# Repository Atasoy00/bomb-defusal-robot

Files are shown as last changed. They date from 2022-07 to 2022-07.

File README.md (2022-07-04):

Bomba İmha Robotu v1.0
======

Bu projede 5 DOF robot kol barındıran hareketli bir sistem tasarımı yapılmıştır.



## # Robot Kol

- Robot kol 5 DOF hareket eksenine sahiptir.
- Ana ve ara eklem servolarının hareketinde ters kinematik denklemler kullanılmıştır.
- Robot kolun gövde bağlantı bölümünde bir adet rulman kullanılarak sistem bu rulman üzerine oturtulmuştur
- Küçük güçte bir servo kullanılarak tüm sistem rahatça döndürülebilmektedir.
- Robot kol 200g'a kadar ağırlıktaki yükleri sorunsuz kaldırabilmektedir



## # Palet

- Motorlardan palete 1:256 oranlı redüktör tasarlanmıştır.
- Yüksek güç üreten redüktör için 30 parça kaymaz palet tasarlanmıştır.
- 6x2 destek tekerleri ile palet sabitlenmiştir.
- Sistemin gücü 12V 9600 rpm çift motorla sağlanmaktadır.  



## # Kontrol Seçenekleri

### 1. TCP Bağlantısı ile Gamepad Kontrolü

- Robot başlatılmadan önce RC kumanda kapalı ise TCP ağına bağlanır.
- TCP/IP bağlantısı kullanılarak gönderilen mesaj kontrol edilmektedir.
- Statik IP adresi kullanılarak adres sabitlenmiştir.
- PC üzerinden kontrol için Python ile TCP kontrol uygulaması yazılmıştır.
- Bilgisayar klavyesinin yetersizliğinden dolayı gamepad driver'ı eklenmiştir.
- Gamepad üzerinden alınan kontroller bir mesaj haline getirilerek gönderilmektedir.



### 2. RC Kumanda Kontrolü

- Robot başlatılmadan önce kumanda açık ise RC kumanda üzerinden kontrol alır.
- Kullanıcıya kontrol alternatifi sunularak RC alıcı entegre edilmiştir.
- RC Kumanda 2km'ye kadar kontrol mesafesini desteklemektedir.
- Kumandadan verilen kontroller daha hızlı ve doğrudur.
- Kumanda üzerinde yeterince kontrol kanalı olmadığı için switch ile sürüş ve robot kol modları arasında geçiş yapılabilmektedir.
- Ters kinematik özelliği kumanda üzerinden açılıp kapanabilmektedir. 



## # Elektronik Devre Şeması



## # Üretim

Projede kullanılan tüm parçalar piyasada kolayca bulunabilen fiyat performans ürünleridir. Geri kalan parçalar açık kaynaklı şekilde proje dosyalarında .stl formatında sunulmuştur. 3B baskı yöntemleri ile parçalar elde edilebilir, hatta eklemeler yapılarak farklı görevlere yönelik tasarımlar oluşturulabilir. Gerekli parçaların üretimi ve temini sonrası kolayca bir araya getirilebilir ve kodu yüklenerek çalışır hale getirilebiliir. 



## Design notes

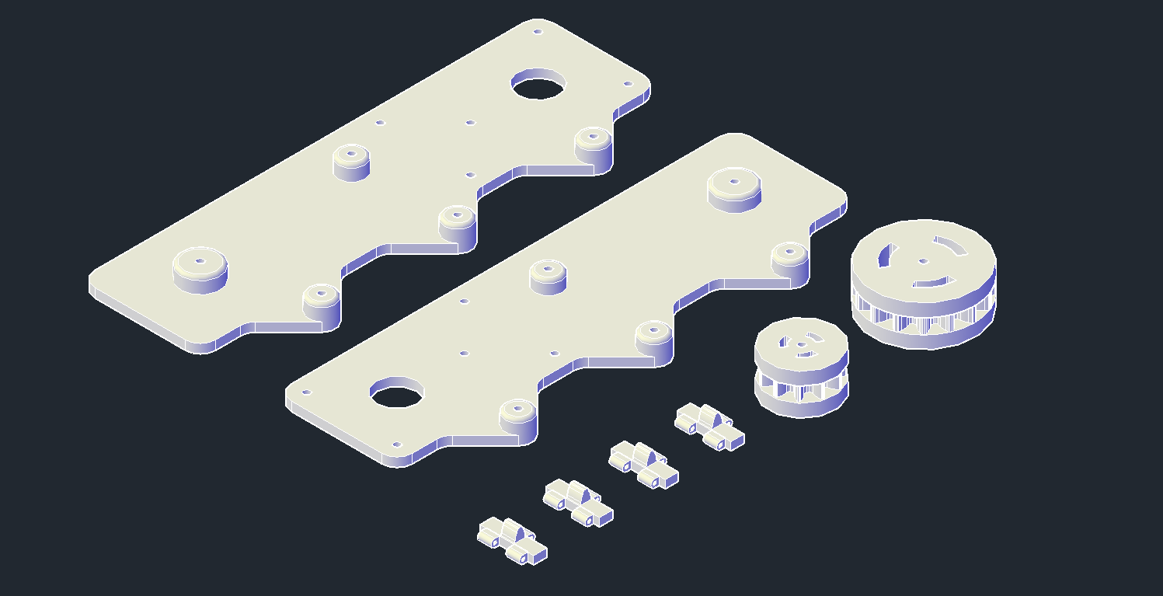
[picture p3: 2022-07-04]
Modellemeler/Resimler/palet_sistemleri.png

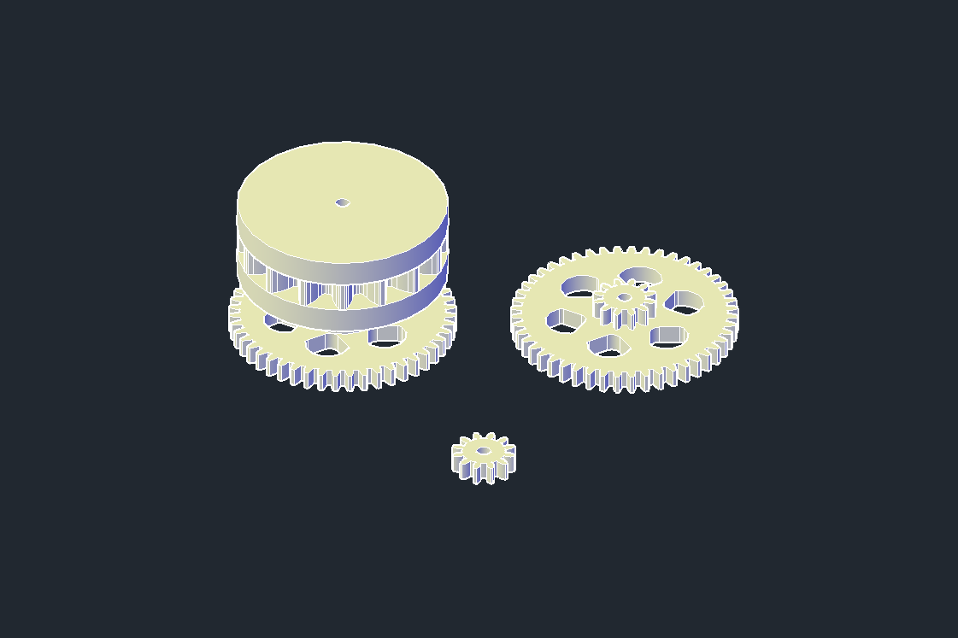
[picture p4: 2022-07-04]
Modellemeler/Resimler/bykdişli_kçkdişli_anatekerdişlisi.png

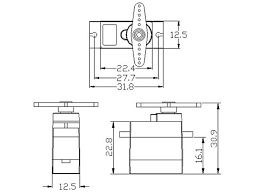
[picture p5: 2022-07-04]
Yardımcı/sg90-teknik çizim.jpg

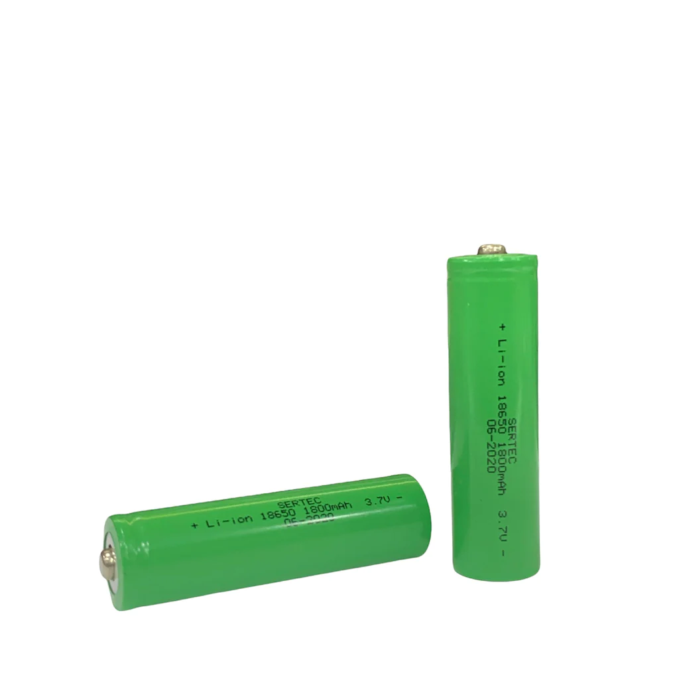
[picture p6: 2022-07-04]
Malzemeler/Resimler/1800mAh 18650 Li-on Pil.jpg

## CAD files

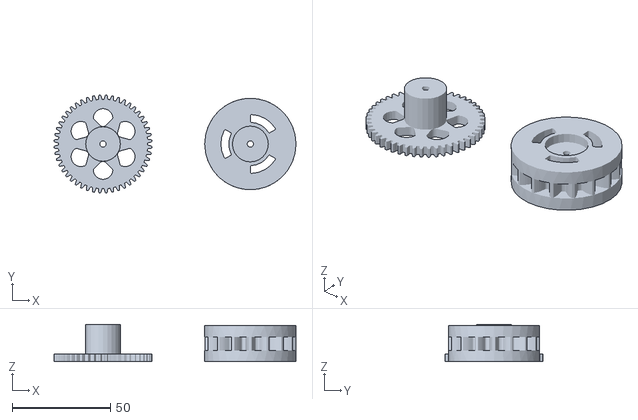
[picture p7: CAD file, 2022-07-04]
Modellemeler/PaletDişliTeker.stl
123.2 x 49.9 x 19.0

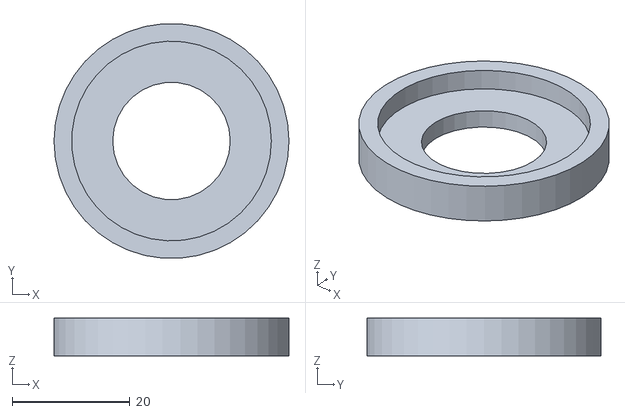
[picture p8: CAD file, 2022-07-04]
Modellemeler/Rulman Şasisi/Rulman Şasisi üst .stl
40.0 x 39.9 x 6.40

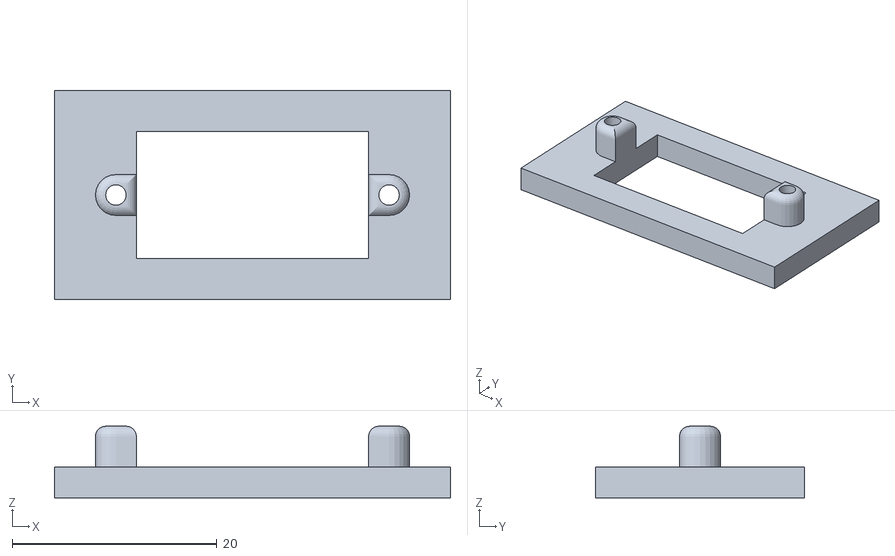
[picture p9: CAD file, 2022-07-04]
Modellemeler/Servo Ekipmanları/Servo Tutucu dnm1.stl
38.7 x 20.4 x 7.00

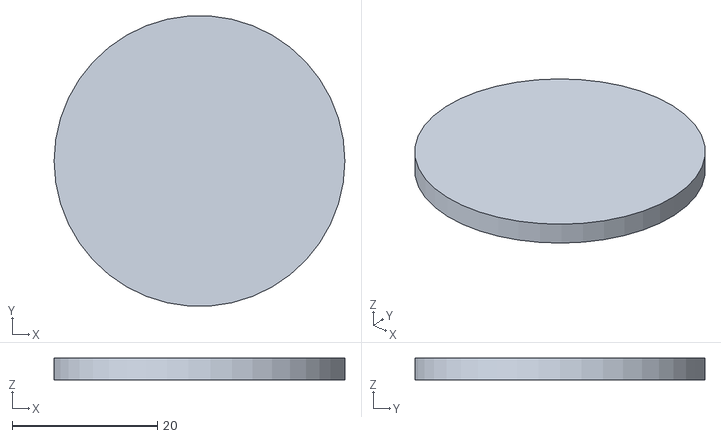
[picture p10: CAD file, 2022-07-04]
Modellemeler/Rulman Şasisi/Rulman Şasisi üst kapak.stl
40.0 x 39.9 x 3.00

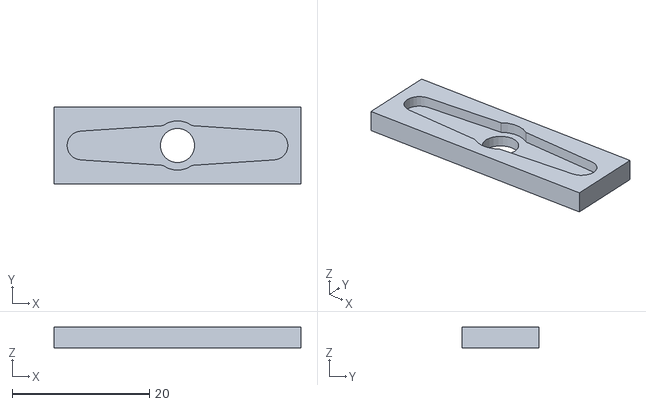
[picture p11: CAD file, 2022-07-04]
Modellemeler/Servo Ekipmanları/Servo Ucu 2 eksen dnm1.stl
36.0 x 11.2 x 3.00

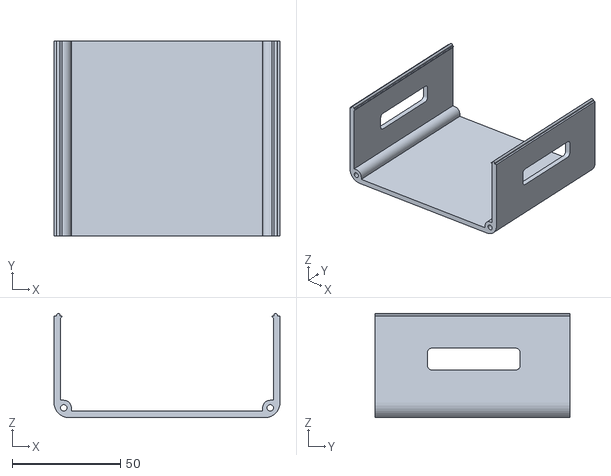
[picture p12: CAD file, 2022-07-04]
Modellemeler/yatay_PaletAraKutu.stl
104.4 x 90.0 x 48.1

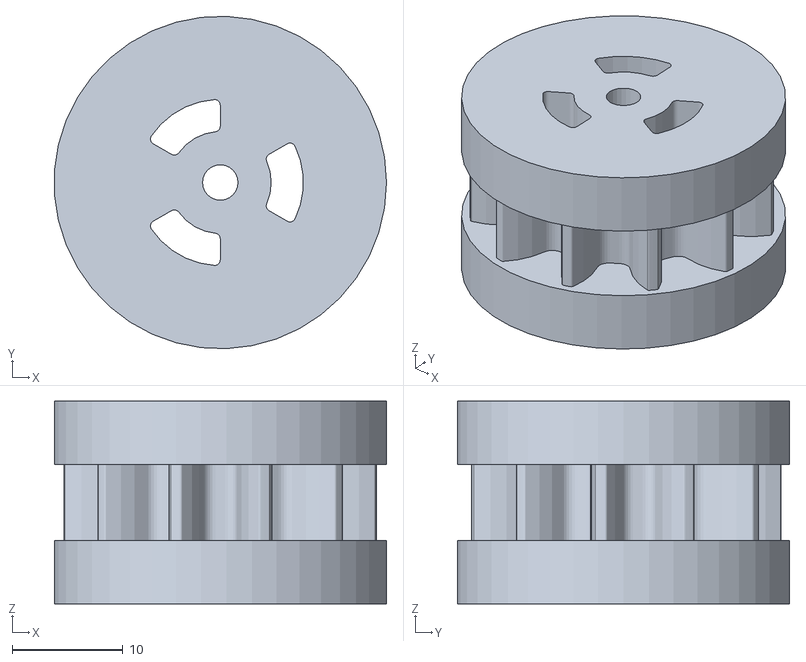
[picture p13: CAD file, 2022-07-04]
Modellemeler/destekTekerDnm1stl.stl
30.0 x 30.0 x 18.3

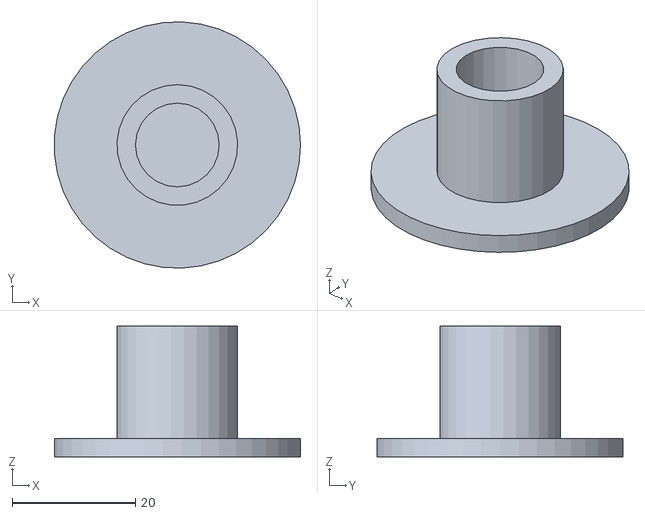
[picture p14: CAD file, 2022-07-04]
Modellemeler/Rulman Şasisi/Rulman Şasisi mili.stl
39.9 x 40.0 x 21.2

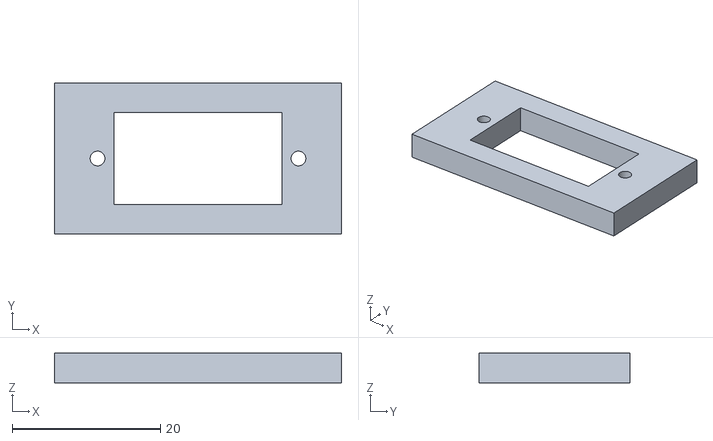
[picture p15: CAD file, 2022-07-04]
Modellemeler/Servo Ekipmanları/Servo Tutucu dnm2.stl
38.7 x 20.4 x 4.00

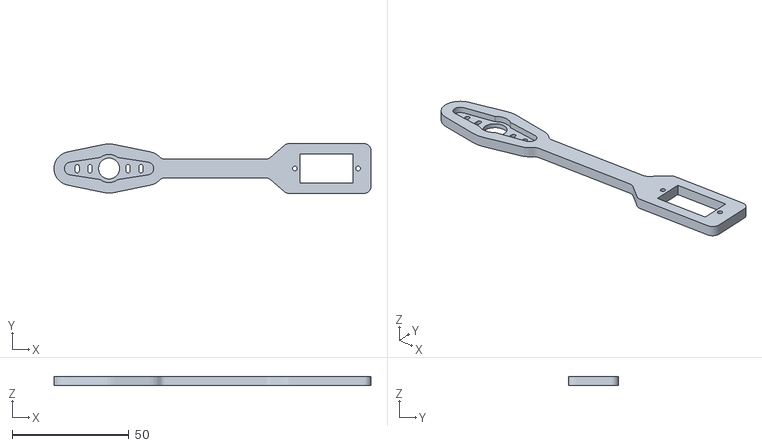
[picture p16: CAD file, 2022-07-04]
Modellemeler/KolServoTutucu dnm2.stl
135.8 x 21.4 x 4.00

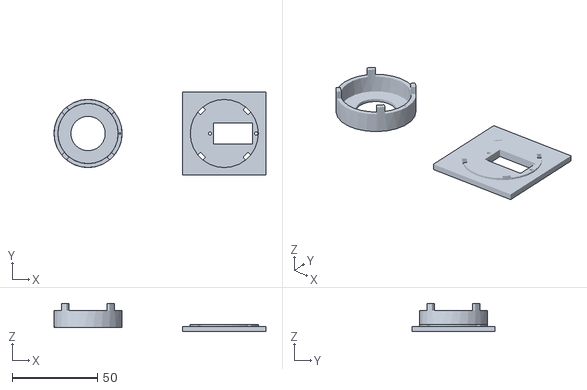
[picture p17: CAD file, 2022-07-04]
Modellemeler/Rulman Şasisi/Rulman Şasisi üst ve kapak 2.stl
124.5 x 49.0 x 16.5

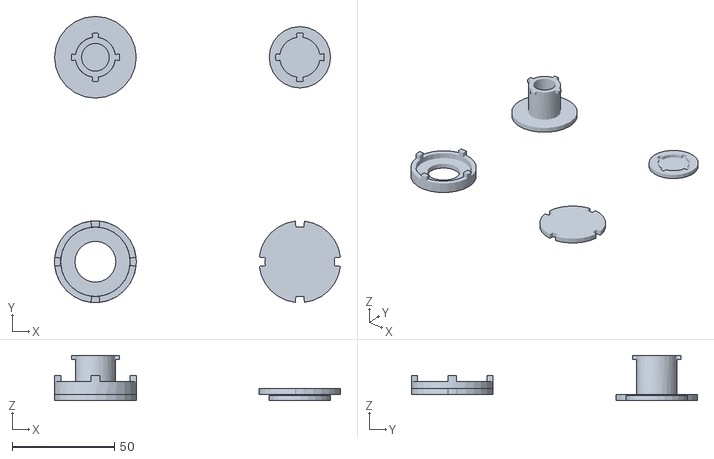
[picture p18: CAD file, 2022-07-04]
Modellemeler/Rulman Şasisi/Rulman Şasisi 2_4 parça.stl
139.9 x 140.0 x 22.2

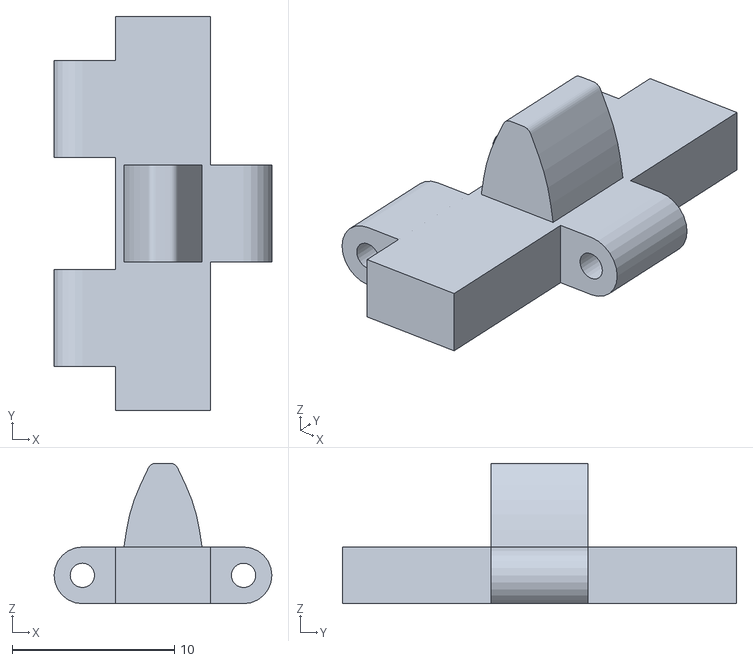
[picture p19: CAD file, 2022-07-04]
Modellemeler/x1_Palet 2.stl
13.4 x 24.3 x 8.66

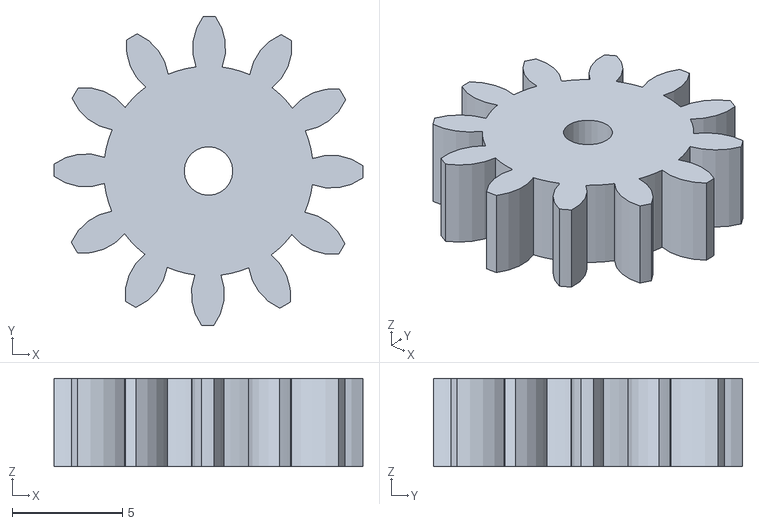
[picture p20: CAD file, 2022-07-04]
Modellemeler/12DüzDişli.stl
14.0 x 14.0 x 4.00

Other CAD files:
Modellemeler/Dişli Hesapları/cark_61 (1).dwg
Modellemeler/Rulman Şasisi/Rulman Şasisi iç kapak.stl
Modellemeler/alt kol.stl
Modellemeler/Rulman Şasisi/Rulman Şasisi mili 2.stl
Modellemeler/12to48Disli.stl
Modellemeler/BüyükDestekTeker -2H32m.stl
Modellemeler/BüyükDestekTeker.stl
Modellemeler/GearBoxTopCover.stl
Modellemeler/KapakPaletAraKutu.stl
Modellemeler/KolServoTutucu dnm1.stl
Modellemeler/MotorluDnm1.stl
Modellemeler/Parmak dnm1.stl
Modellemeler/SAGPaletTutacak.stl
Modellemeler/SAG_SOLMotorTutacak.stl
Modellemeler/SOLPaletTutacak -4H32m.stl
Modellemeler/SOLPaletTutacak.stl
Modellemeler/dikey_PaletAraKutu.stl
Modellemeler/x5_Palet2.stl

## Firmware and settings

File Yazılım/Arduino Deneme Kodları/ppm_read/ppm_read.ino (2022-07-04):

#include <PPMReader.h>
#include <Servo.h>

// Initialize a PPMReader on digital pin 3 with 6 expected channels.
byte interruptPin = 3;
byte channelAmount = 6;
PPMReader ppm(interruptPin, channelAmount);

Servo servo1;
Servo servo2;
Servo servo3;
Servo servo4;
Servo servo5;
Servo servo6;

//-----Kanal Tepe Değerleri-------Kanal Taban Değerleri-----
unsigned int ch1MAX = 2000; unsigned int ch1MIN = 1055; 
unsigned int ch2MAX = 2000; unsigned int ch2MIN = 1045; 
unsigned int ch3MAX = 1985; unsigned int ch3MIN = 1105; 
unsigned int ch4MAX = 2050; unsigned int ch4MIN = 950; 
unsigned int ch5MAX = 2050; unsigned int ch5MIN = 950; 
unsigned int ch6MAX = 2050; unsigned int ch6MIN = 950; 

//-----Servoya Yazılacak Degerler-----
int ch1SER;
int ch2SER;
int ch3SER;
int ch4SER;
int ch5SER;
int ch6SER;


void setup() {
    Serial.begin(115200);

//    servo1.attach(8);
//    servo2.attach(9);
//    servo3.attach(10);
//    servo4.attach(11);
//    servo5.attach(12);
//    servo6.attach(13);

    pinMode(10, OUTPUT);
    pinMode(11, OUTPUT);
    pinMode(12, OUTPUT);
    pinMode(13, OUTPUT);

    servo1.attach(8);
    servo2.attach(9);

}

void loop() {

    unsigned int ch1RAW = ppm.latestValidChannelValue(1, 0);
    unsigned int ch2RAW = ppm.latestValidChannelValue(2, 0);
    unsigned int ch3RAW = ppm.latestValidChannelValue(3, 0);
    unsigned int ch4RAW = ppm.latestValidChannelValue(4, 0);
    unsigned int ch5RAW = ppm.latestValidChannelValue(5, 0);
    unsigned int ch6RAW = ppm.latestValidChannelValue(6, 0);


    if (ch1RAW > ch1MIN && ch1RAW < ch1MAX){ ch1SER = map(ch1RAW, ch1MIN, ch1MAX, 0, 180);}
    else{if(ch1RAW < ch1MIN){ch1SER=0;}if(ch1RAW > ch1MIN){ch1SER=180;}}
    if (ch2RAW > ch2MIN && ch2RAW < ch2MAX){ ch2SER = map(ch2RAW, ch2MIN, ch2MAX, 0, 180);}
    else{if(ch2RAW < ch2MIN){ch2SER=0;}if(ch2RAW > ch2MIN){ch2SER=180;}}
    if (ch3RAW > ch3MIN && ch3RAW < ch3MAX){ ch3SER = map(ch3RAW, ch3MIN, ch3MAX, 0, 180);}
    else{if(ch3RAW < ch3MIN){ch3SER=0;}if(ch3RAW > ch3MIN){ch3SER=180;}} 
    if (ch4RAW > ch4MIN && ch4RAW < ch4MAX){ ch4SER = map(ch4RAW, ch4MIN, ch4MAX, 0, 180);}
    else{if(ch4RAW < ch4MIN){ch4SER=0;}if(ch4RAW > ch4MIN){ch4SER=180;}}
    if (ch5RAW > ch5MIN && ch5RAW < ch5MAX){ ch5SER = map(ch5RAW, ch5MIN, ch5MAX, 0, 180);}
    else{if(ch5RAW < ch5MIN){ch5SER=0;}if(ch5RAW > ch5MIN){ch5SER=180;}}
    if (ch6RAW > ch6MIN && ch6RAW < ch6MAX){ ch6SER = map(ch6RAW, ch6MIN, ch6MAX, 0, 180);}
    else{if(ch6RAW < ch6MIN){ch6SER=0;}if(ch6RAW > ch6MIN){ch6SER=180;}}

//    servo1.write(ch1SER);
//    servo2.write(ch2SER);
//    servo3.write(ch3SER);
//    servo4.write(ch4SER);
//    servo5.write(ch5SER);
//    servo6.write(ch6SER);

    byte IN1,IN2,IN3,IN4,ENA,ENB;

    if     ((ch1SER>45  && ch1SER<135) && (ch2SER>45  && ch2SER<135))   {IN1=0;IN2=0;ENA=0;    IN3=0;IN4=0;ENB=0;  }//dur
    else if((ch1SER>45  && ch1SER<135) && (ch2SER>135 && ch2SER<200))   {IN1=1;IN2=0;ENA=180;  IN3=1;IN4=0;ENB=180;}//ileri
    else if((ch1SER>45  && ch1SER<135) && (ch2SER>-20 && ch2SER<45))    {IN1=0;IN2=1;ENA=180;  IN3=0;IN4=1;ENB=180;}//geri
    else if((ch1SER>-20 && ch1SER<45)  && (ch2SER>45  && ch2SER<135))   {IN1=1;IN2=0;ENA=180;  IN3=0;IN4=1;ENB=180;}//sağ
    else if((ch1SER>135 && ch1SER<200) && (ch2SER>45  && ch2SER<135))   {IN1=0;IN2=1;ENA=180;  IN3=1;IN4=0;ENB=180;}//sol
    else if((ch1SER>-20 && ch1SER<45)  && (ch2SER>135 && ch2SER<200))   {IN1=1;IN2=0;ENA=180;  IN3=0;IN4=0;ENB=0;  }//sağ ileri
    else if((ch1SER>135 && ch1SER<200) && (ch2SER>135 && ch2SER<200))   {IN1=0;IN2=0;ENA=0;    IN3=1;IN4=0;ENB=180;}//sol ileri
    else if((ch1SER>-20 && ch1SER<45)  && (ch2SER>-20 && ch2SER<45))    {IN1=0;IN2=1;ENA=180;  IN3=0;IN4=0;ENB=0;  }//sağ geri
    else if((ch1SER>135 && ch1SER<200) && (ch2SER>-20 && ch2SER<45))    {IN1=0;IN2=0;ENA=0;    IN3=0;IN4=1;ENB=180;}//sol geri
    else                                                                {IN1=0;IN2=0;ENA=0;    IN3=0;IN4=0;ENB=0;  }//dur


    digitalWrite(10,IN1);
    digitalWrite(11,IN2);
    digitalWrite(12,IN3);
    digitalWrite(13,IN4);

    servo1.write(ENA);
    servo2.write(ENB);
    


    Serial.print(ch1RAW); Serial.print('\t'); Serial.print(IN1); Serial.print('\t'); 
    Serial.print(ch2RAW); Serial.print('\t'); Serial.print(IN2); Serial.print('\t'); 
    Serial.print(ch3RAW); Serial.print('\t'); Serial.print(IN3); Serial.print('\t');  
    Serial.print(ch4RAW); Serial.print('\t'); Serial.print(IN4); Serial.print('\t'); 
    Serial.print(ch5RAW); Serial.print('\t'); Serial.print(ENA); Serial.print('\t'); 
    Serial.print(ch6RAW); Serial.print('\t'); Serial.print(ENB); Serial.println();
    delay(20);
}

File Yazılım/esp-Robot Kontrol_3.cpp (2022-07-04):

#include <Arduino.h>
#include "WiFi.h"
#include <Wire.h>
#include <Adafruit_PWMServoDriver.h>
#include <PPMReader.h>

const char* ssid = "***";
const char* password = "***";

//const char* ssid = "***";
//const char* password = "***";

IPAddress staticIP(192, 168, 1, 166);
IPAddress gateway(192, 168, 1, 1);
IPAddress subnet(255, 255, 255, 0);
IPAddress dns(192, 168, 1, 1);

WiFiServer wifiServer(80);

int joy[4];
int buton[8];
int tusx,tusy;

// Initialize a PPMReader on digital pin 3 with 6 expected channels.
byte interruptPin = 4;
byte channelAmount = 6;
PPMReader ppm(interruptPin, channelAmount);

Adafruit_PWMServoDriver pwm = Adafruit_PWMServoDriver();

#define SERVOMIN  100 // This is the 'minimum' pulse length count (out of 4096)
#define SERVOMAX  450 // This is the 'maximum' pulse length count (out of 4096)
#define SERVO_FREQ 50 // Analog servos run at ~50 Hz updates

uint8_t servonum = 0;

int x,y;
double pi = 3.1415926535; 
double q1,q2,q1_deg,q2_deg;
uint l1=76,l2=174; //76,174
double foo1,bar1,foo2,bar2,foo3;
int move;

//-----Kanal Tepe Değerleri-------Kanal Taban Değerleri-----
unsigned int ch1MAX = 2000; unsigned int ch1MIN = 1050; 
unsigned int ch2MAX = 2000; unsigned int ch2MIN = 1045; 
unsigned int ch3MAX = 1985; unsigned int ch3MIN = 1105; 
unsigned int ch4MAX = 2050; unsigned int ch4MIN = 950; 
unsigned int ch5MAX = 2050; unsigned int ch5MIN = 950; 
unsigned int ch6MAX = 2050; unsigned int ch6MIN = 950; 

//-----Servoya Yazılacak Degerler-----
int ch1SER  =275;
int ch2SER  =430;
int ch2SER1 =430;
int ch3SER  =180;
int ch3SER1 =180;
int ch4SER  =260;
int ch5SER  =110;
int ch6SER  =275;

char rcKumanda = 0;

void setup() {
 
  Serial.begin(115200);

  //ch3 ppm okuması
  unsigned int ch3RAW = ppm.latestValidChannelValue(3, 0);

  Serial.println();
  if(ch3RAW>0){Serial.println("RC Kumanda Aktif"); rcKumanda=1;}
  else{Serial.println("Wifi Kontrol Modu");rcKumanda=0;}
 
  if(!(rcKumanda)) //Wifi Kontrol Modu
  {

    delay(1000);

    if (WiFi.config(staticIP, gateway, subnet, dns, dns) == false) 
    {
      Serial.println("Configuration failed.");
    }

    WiFi.begin(ssid, password);

    while (WiFi.status() != WL_CONNECTED) {
      delay(1000);
      Serial.println("Connecting to WiFi..");
    }

    Serial.println("Connected to the WiFi network");
    Serial.println(WiFi.localIP());

    wifiServer.begin();

  }

  pwm.begin();
  pwm.setOscillatorFrequency(27000000);
  pwm.setPWMFreq(SERVO_FREQ);  // Analog servos run at ~50 Hz updates
  delay(10);

  pinMode(26, OUTPUT);
  pinMode(25, OUTPUT);
  pinMode(33, OUTPUT);
  pinMode(32, OUTPUT);

}
 
void loop() {
 
  if(!(rcKumanda))
  {
    WiFiClient client = wifiServer.available();
    int data[14];

    // kontrol okuma işlemi
  
    if (client) {
      while (client.connected()) {
        while (client.available()>0) {

          for(int i=0;i<14;i++)
          {
            int c = client.read();
            data[i] = c-53;
          }

          joy[0] = data[0]; joy[1] = data[1]; joy[2] = data[2]; joy[3] = data[3];
          buton[0] = data[4]; buton[1] = data[5]; buton[2] = data[6];  buton[3] = data[7]; 
          buton[4] = data[8]; buton[5] = data[9]; buton[6] = data[10]; buton[7] = data[11];
          tusx=data[12]; tusy=data[13];
          
          // servo değer hesaplamaları ----------------------------------------------------------------------------------------------

          move=3;
          //kavrama
          if(buton[0]){/*75*/ ch5SER=284;}
          if(buton[1]){/*50*/ ch5SER=197;}
          if(buton[2]){/*0*/  ch5SER=SERVOMIN+10;}
          if(buton[3]){/*100*/ch5SER=SERVOMAX-80;}
          
          //bilek_servo
          if(buton[4]){/*sola_don*/ch4SER+=move;if(ch4SER>SERVOMAX){ch4SER=SERVOMAX;}}
          if(buton[5]){/*saga_don*/ch4SER-=move;if(ch4SER<SERVOMIN){ch4SER=SERVOMIN;}}       

          //doner_servo
          if(buton[6]){/*sola_don*/ch1SER+=move;if(ch1SER>SERVOMAX){ch1SER=SERVOMAX;}}
          if(buton[7]){/*saga_don*/ch1SER-=move;if(ch1SER<SERVOMIN){ch1SER=SERVOMIN;}}

          //yukseklik
          if     (tusy == 1){/*yukarı*/ch2SER1+=move;if(ch2SER1>SERVOMAX){ch2SER1=SERVOMAX;}}
          else if(tusy ==-1){/*asagı*/ ch2SER1-=move;if(ch2SER1<SERVOMIN){ch2SER1=SERVOMIN;}}

          //derinlik
          if     (joy[3] ==-1){/*ileri*/ch3SER1+=move;if(ch3SER1>SERVOMAX){ch3SER1=SERVOMAX;}}
          else if(joy[3] == 1){/*geri*/ ch3SER1-=move;if(ch3SER1<SERVOMIN){ch3SER1=SERVOMIN;}}


          //Serial.print("ch2SERBBB = "); Serial.println(ch2SER1);
          //Serial.print("ch3SERBBB = "); Serial.println(ch3SER1);

          // sürüş kontrol --------------------------------------------------------------------------------------------------------------
          byte IN1,IN2,IN3,IN4;

          if     ((joy[0]==0)  && (joy[1]==0))   {IN1=0;IN2=0;  IN3=0;IN4=0;}//dur
          else if((joy[0]==0)  && (joy[1]==-1))  {IN1=1;IN2=0;  IN3=1;IN4=0;}//ileri
          else if((joy[0]==0)  && (joy[1]==1))   {IN1=0;IN2=1;  IN3=0;IN4=1;}//geri
          else if((joy[0]==1)  && (joy[1]==0))   {IN1=1;IN2=0;  IN3=0;IN4=1;}//sağ
          else if((joy[0]==-1) && (joy[1]==0))   {IN1=0;IN2=1;  IN3=1;IN4=0;}//sol
          else if((joy[0]==1)  && (joy[1]==-1))  {IN1=1;IN2=0;  IN3=0;IN4=0;}//sağ ileri
          else if((joy[0]==-1) && (joy[1]==-1))  {IN1=0;IN2=0;  IN3=1;IN4=0;}//sol ileri
          else if((joy[0]==1)  && (joy[1]==1))   {IN1=0;IN2=1;  IN3=0;IN4=0;}//sağ geri
          else if((joy[0]==-1) && (joy[1]==1))   {IN1=0;IN2=0;  IN3=0;IN4=1;}//sol geri
          else                                   {IN1=0;IN2=0;  IN3=0;IN4=0;}//dur


          digitalWrite(26,IN3);
          digitalWrite(25,IN4);
          digitalWrite(33,IN1);
          digitalWrite(32,IN2);

          // robot kol kontrolü -------------------------------------------------------------------------------------------------------------


          //Ters Kinematik Denklem

          x = map(ch3SER1, SERVOMIN,SERVOMAX, 70,176);
          y = map(ch2SER1, SERVOMIN,SERVOMAX, 70,176);

          
          //Serial.print("x = "); Serial.println(x);
          //Serial.print("y = "); Serial.println(y);

          //foo1 = (pow(l1,2)+pow(l2,2)-pow(x,2)-pow(y,2)); //yöntem1
          foo3 = (0-pow(l1,2)-pow(l2,2)+pow(x,2)+pow(y,2)); //yöntem2
          bar1 = (2*l1*l2);

          //q2 = pi - acos(foo1/bar1);
          q2 = acos(foo3/bar1);

          foo2 = (l2*sin(q2));
          bar2 = (l1+l2*cos(q2));

          q1 = atan(x/(y+0.0001))-atan(foo2/bar2);

          q1_deg = q1*57.2957795;
          q2_deg = q2*57.2957795;

          q1_deg = map(q1_deg, -90,90, 0,180);

          if(q1_deg>140) q1_deg = q1_deg-180;

          if(q2_deg>165) q2_deg = 165;
      
          //Serial.print("q1 = "); Serial.println(q1_deg);
          //Serial.print("q2 = "); Serial.println(q2_deg);

          //q1_deg = 0;
          //q2_deg = 0;
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
